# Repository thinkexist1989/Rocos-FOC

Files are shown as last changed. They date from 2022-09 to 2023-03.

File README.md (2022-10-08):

# ROCOS FOC *for Motor Control*

:warning:这是一个FOC驱动器项目，目前正在开发中~

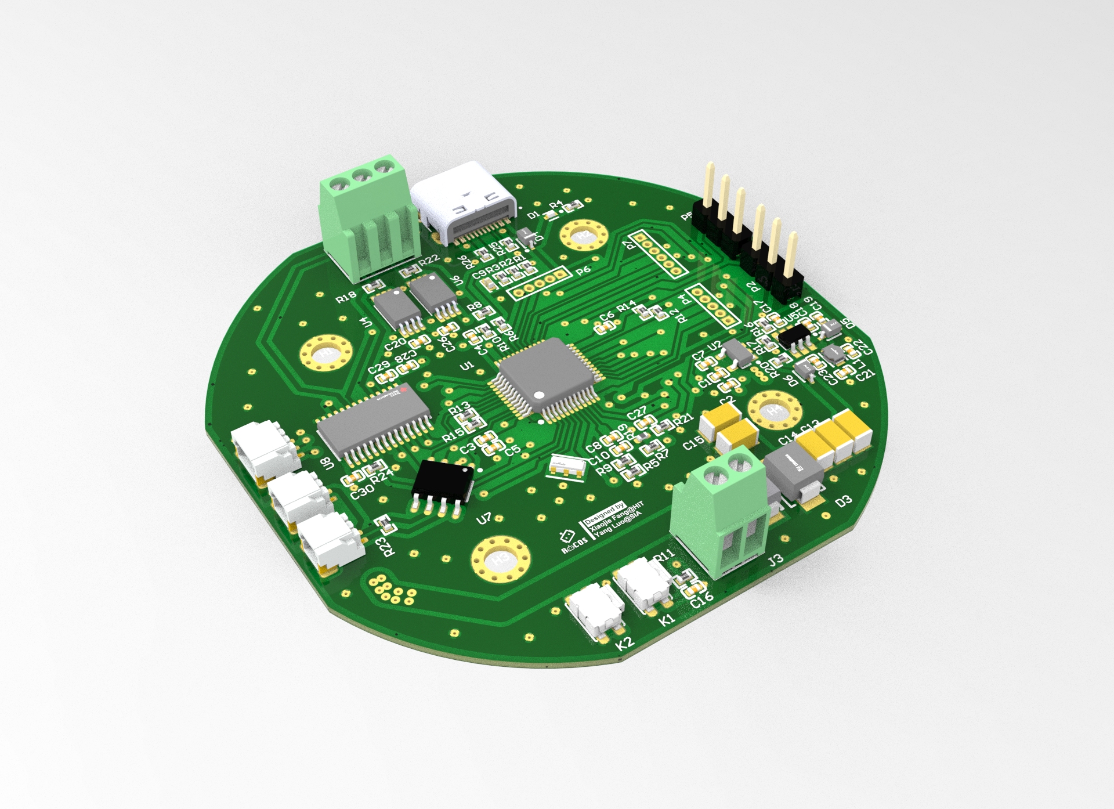
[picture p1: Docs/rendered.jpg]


驱动器采用的方案：

- **电机**：[GB6010云台电机](https://item.taobao.com/item.htm?spm=a1z0d.7625083.1998302264.6.5c5f4e6900plQJ&id=639378697535)，14对极，具体参数如下：
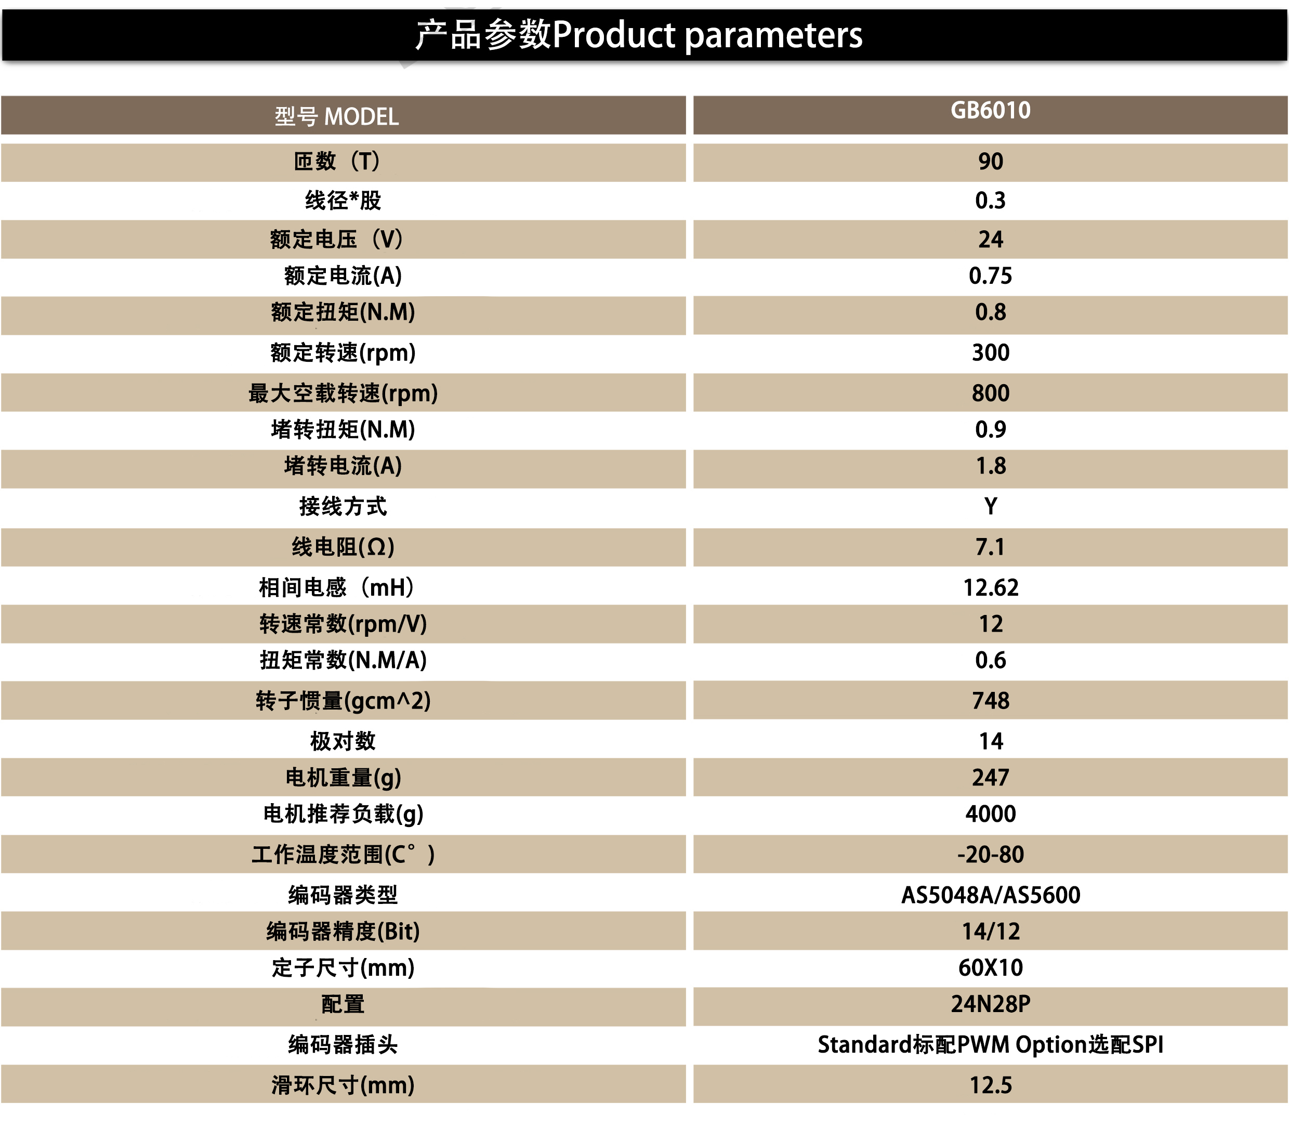
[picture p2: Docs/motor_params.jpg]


- **主控**：STM32F103CBT6
- **位置传感器**：AS5048A，SPI接口
- **驱动**：DRV8313
- **电流传感器**：INA240，线上检测（增益50V/V，采样电阻0.01R）

## 接口及尺寸定义

驱动器可以直接安装在电机尾部（电机尾部自带一块径向充磁的磁铁，AS5048A正对磁铁）

接口方面主要包括：

- USB-C接口（16pin）
- 电机三相接口，KF128-3p
- 电源接口， KF128-2p
- SW调试口， SH1.0-3p
- CAN总线接口，SH1.0-2p

其余引脚通过插针引出使用，具体见下图：

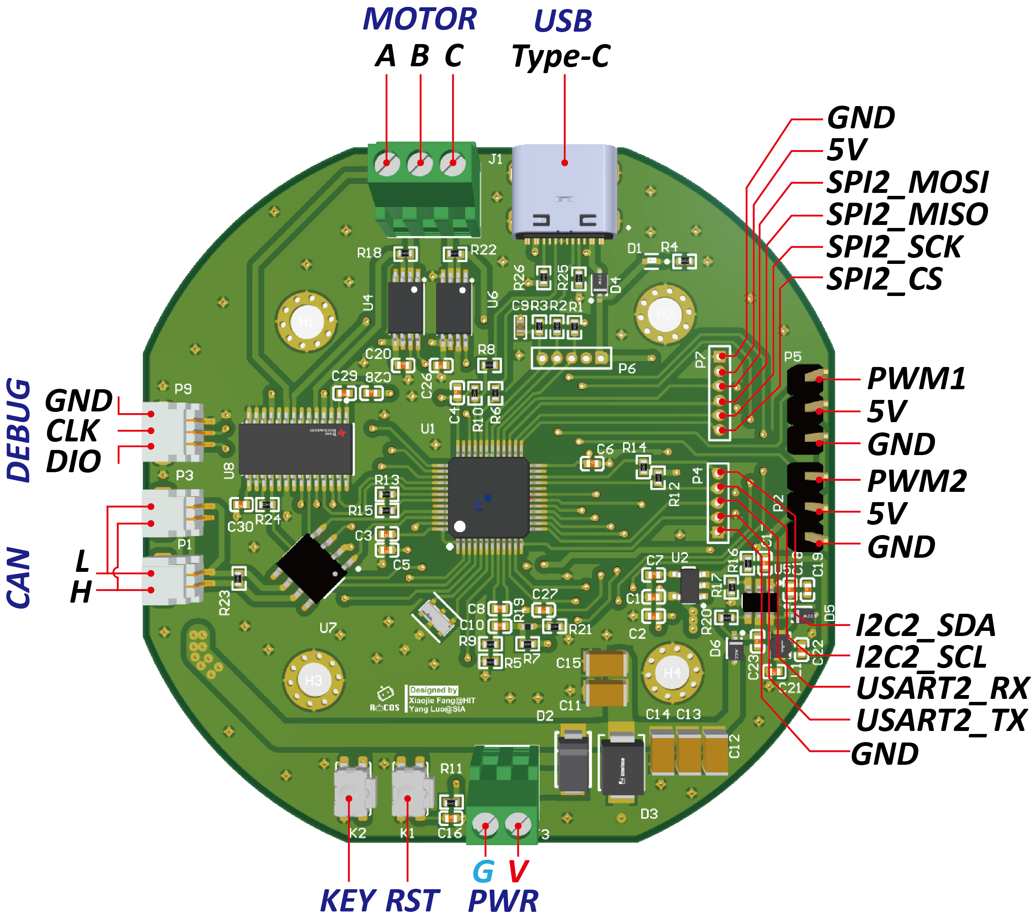
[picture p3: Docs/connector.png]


## 文件夹结构

```bash
Rocos-FOC
 ├── Firmware 驱动器固件代码
       ├── HAL_Version 基于STM32CubeMX和HAL库版本
       └── Platformio_Version 基于Platformio及Arduino版本
 ├── Hardware 硬件设计（原理图和PCB）
 ├── Model 驱动器三维模型Keyshots渲染文件
 ├── Docs  相关资料文档
 └── Utils 相关实用工具

```

## 参考

- [SimpleFOClibrary - Simple Field Oriented Control (FOC) library](https://github.com/simplefoc/Arduino-FOC)
- [Ctrl-FOC-Lite评估套件](https://github.com/peng-zhihui/Ctrl-FOC-Lite)
- [灯哥开源FOC双路无刷电机控制器](https://github.com/ToanTech/Deng-s-foc-controller)
- [dgm 电机驱动器简介](https://github.com/codenocold/dgm)
- [ODrive](https://github.com/odriverobotics/ODrive)

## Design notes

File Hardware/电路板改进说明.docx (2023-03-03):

# Rocos-foc电路改进说明

1. 增加了USB转串口模块，占用了原本留空的UART2接口：
2. 给CAN信号增加了终端电阻的开关，只需拨动开关即可实现工作模式的切换：
3. USB与CAN线增加了差分符号，可以使用altium designer提供的差分布线工具更快布线，并附带耦合检查功能
4. 调整了ABC三相导线的线序，方便布线，交换了原AC两项导线位置
5. 排针全部删去，换成了sh1.0接口
6. 固定孔网络改为NO NET，减少短路风险
7. 改变了按键朝向，方便按动
8. VCC走线大部分移到内电层，减少表层布线压力
9. 给晶振加了包地和铺铜挖空
10. 所有接口在正面标明了各引脚定义，方便查看

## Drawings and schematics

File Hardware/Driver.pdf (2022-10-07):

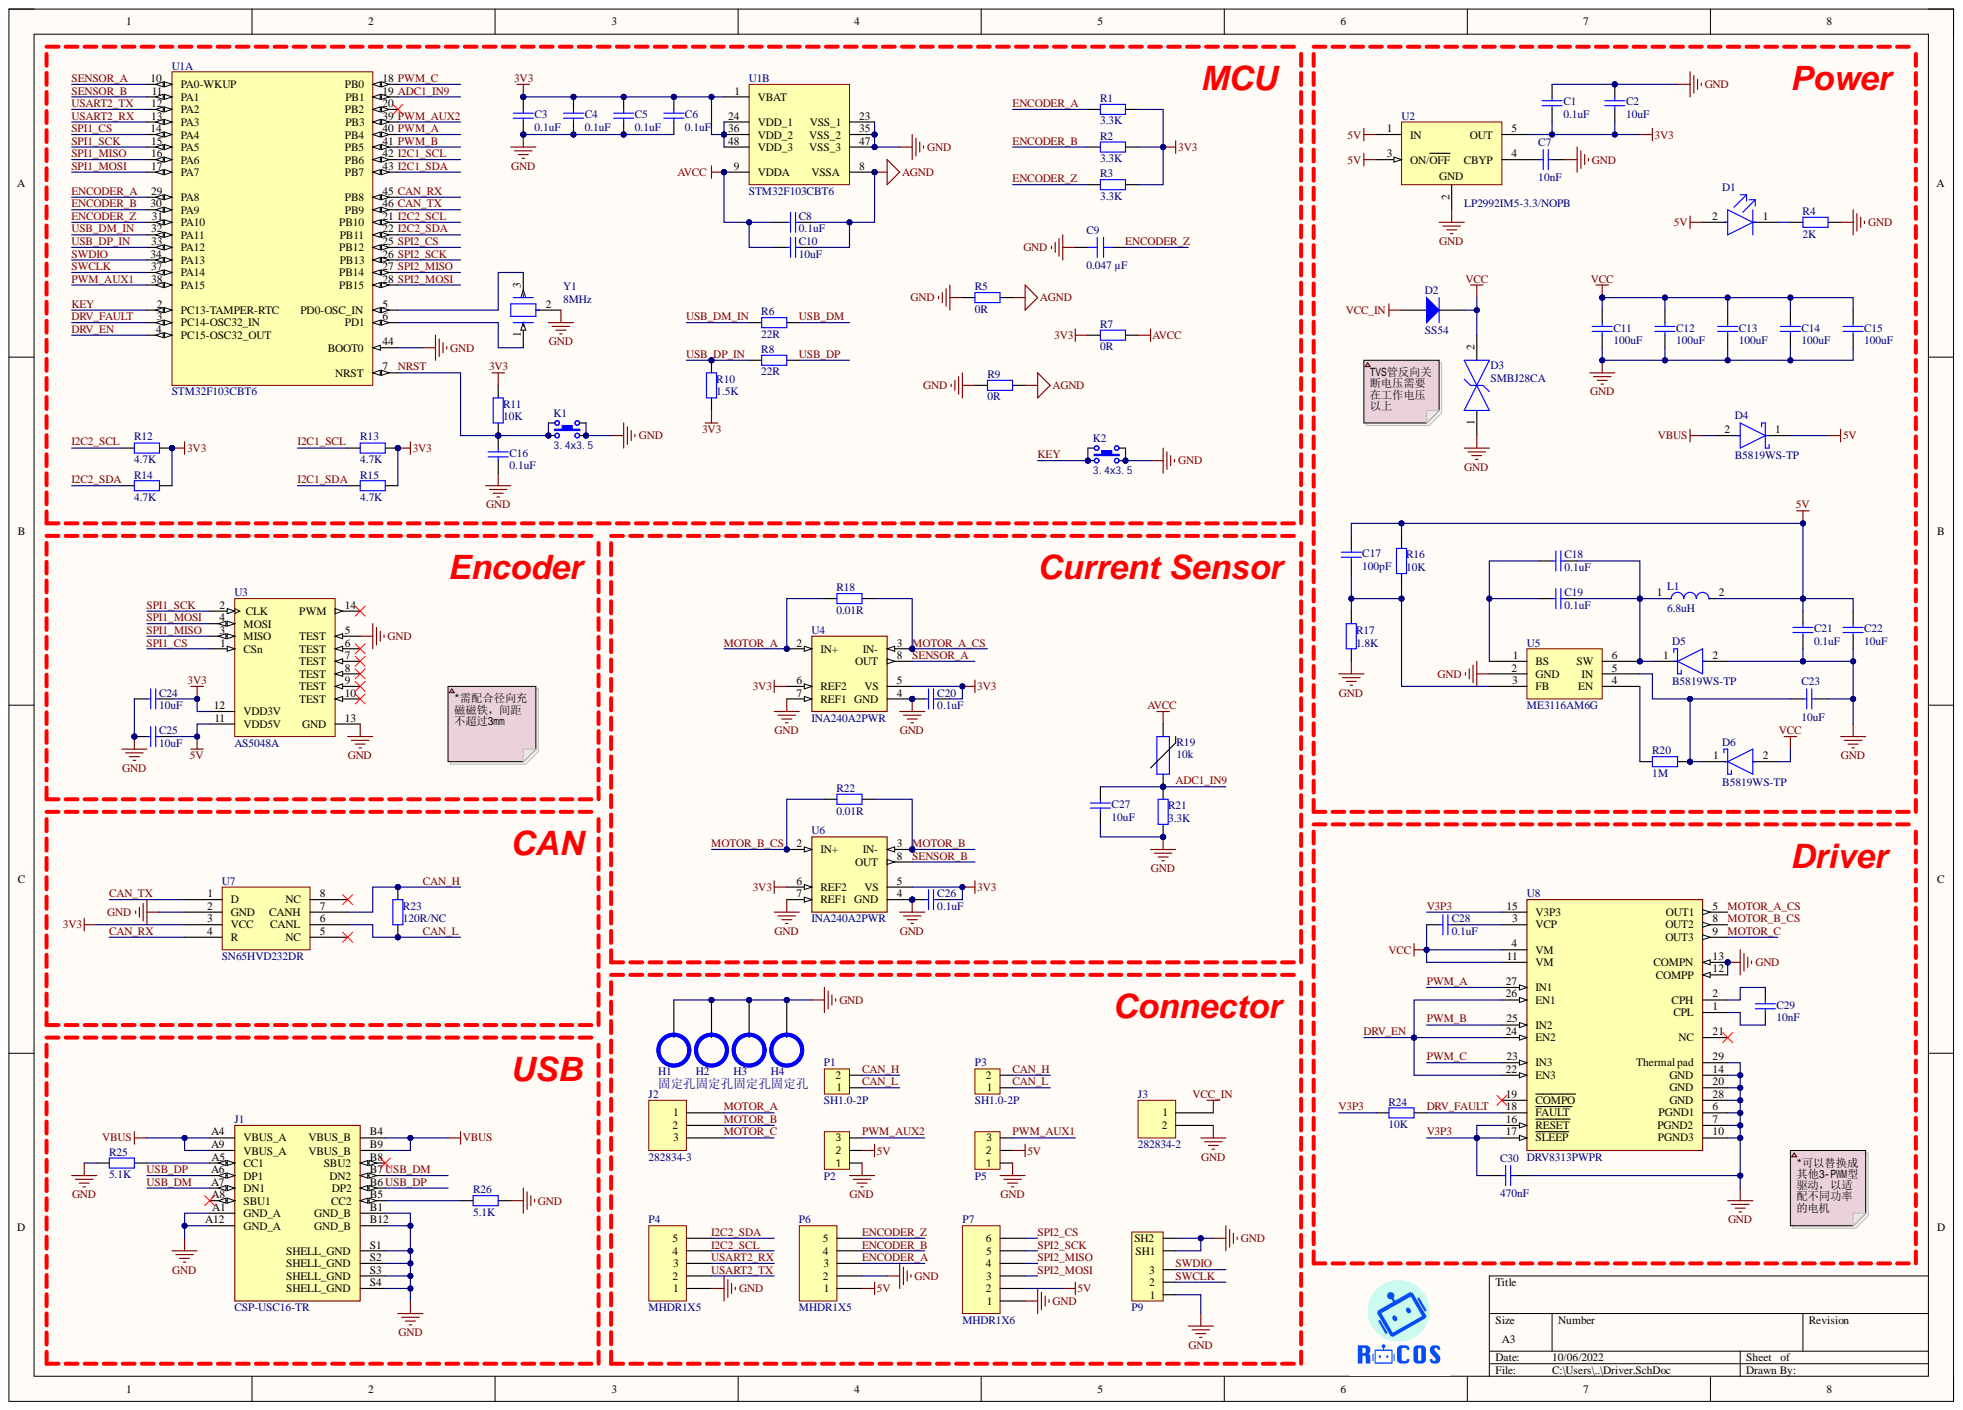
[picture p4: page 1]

TVS管反向关 断电压需要 在工作电压 以上

需配合径向充 磁磁铁，间距 不超过 mm

可以替换成 其他 PWM型 驱动，以适

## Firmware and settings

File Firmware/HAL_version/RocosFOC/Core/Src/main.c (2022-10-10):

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
/* Includes ------------------------------------------------------------------*/
#include "main.h"
#include "usb_device.h"

/* USER CODE BEGIN Includes */
#include "usbd_cdc_if.h"
/* USER CODE END Includes */

 ADC_HandleTypeDef hadc1;
DMA_HandleTypeDef hdma_adc1;

RTC_HandleTypeDef hrtc;

SPI_HandleTypeDef hspi1;

TIM_HandleTypeDef htim1;
TIM_HandleTypeDef htim2;
TIM_HandleTypeDef htim3;
TIM_HandleTypeDef htim4;

/* USER CODE BEGIN PV */

//!< for timestamp_us
unsigned long timer_counter = 0;

/* USER CODE END PV */

void SystemClock_Config(void);
static void MX_GPIO_Init(void);
static void MX_ADC1_Init(void);
static void MX_SPI1_Init(void);
static void MX_TIM1_Init(void);
static void MX_TIM3_Init(void);
static void MX_DMA_Init(void);
static void MX_TIM4_Init(void);
static void MX_RTC_Init(void);
static void MX_TIM2_Init(void);
/* USER CODE BEGIN PFP */
static void USB_Status_Init(void);
/* USER CODE END PFP */

/**
  * @brief  The application entry point.
  * @retval int
  */
int main(void)
{
  /* MCU Configuration--------------------------------------------------------*/

  /* Reset of all peripherals, Initializes the Flash interface and the Systick. */
  HAL_Init();

  /* Configure the system clock */
  SystemClock_Config();

  /* USER CODE BEGIN SysInit */
  USB_Status_Init();
  /* USER CODE END SysInit */

  /* Initialize all configured peripherals */
  MX_GPIO_Init();
  MX_ADC1_Init();
  MX_SPI1_Init();
  MX_TIM1_Init();
  MX_TIM3_Init();
  MX_USB_DEVICE_Init();
  MX_DMA_Init();
  MX_TIM4_Init();
  MX_RTC_Init();
  MX_TIM2_Init();
  /* USER CODE BEGIN 2 */
  //!< start pwm
  HAL_TIM_PWM_Start(&htim3, TIM_CHANNEL_1); // Motor A
  HAL_TIM_PWM_Start(&htim3, TIM_CHANNEL_2); // Motor B
  HAL_TIM_PWM_Start(&htim3, TIM_CHANNEL_3); // Motor C
  //!< for delay_us
  HAL_TIM_Base_Start(&htim2);
    HAL_TIM_Base_Start_IT(&htim4);
  TaskSetup();

  /* USER CODE END 2 */

  /* Infinite loop */
  /* USER CODE BEGIN WHILE */
  while (1)
  {
    /* USER CODE END WHILE */

    /* USER CODE BEGIN 3 */
    TaskDo();

  }
  /* USER CODE END 3 */
}

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
/* USER CODE BEGIN 4 */
static void USB_Status_Init(void) {
    GPIO_InitTypeDef GPIO_InitStruct = {0};

    /* GPIO Ports Clock Enable */
    __HAL_RCC_GPIOA_CLK_ENABLE();

    /*Configure GPIO pin Output Level */
    HAL_GPIO_WritePin(GPIOA, GPIO_PIN_11 | GPIO_PIN_12, GPIO_PIN_RESET);

    /*Configure GPIO pin : W25Q256_CS_Pin */
    GPIO_InitStruct.Pin = GPIO_PIN_11 | GPIO_PIN_12;
    GPIO_InitStruct.Mode = GPIO_MODE_OUTPUT_PP;
    GPIO_InitStruct.Pull = GPIO_PULLDOWN;
    GPIO_InitStruct.Speed = GPIO_SPEED_FREQ_LOW;
    HAL_GPIO_Init(GPIOA, &GPIO_InitStruct);

    HAL_Delay(20);
}

void HAL_TIM_PeriodElapsedCallback(TIM_HandleTypeDef *htim) {
//    usb_printf("timer_counter: %d", timer_counter);
    if(htim->Instance == htim4.Instance) {
        timer_counter ++;
    }
}

void _writeDutyCycle3PWM(float dc_a, float dc_b, float dc_c) {
    __HAL_TIM_SetCompare(&htim3, TIM_CHANNEL_1, dc_a*PWM_RANGE);
    __HAL_TIM_SetCompare(&htim3, TIM_CHANNEL_2, dc_b*PWM_RANGE);
    __HAL_TIM_SetCompare(&htim3, TIM_CHANNEL_3, dc_c*PWM_RANGE);
}

/* USER CODE END 4 */
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


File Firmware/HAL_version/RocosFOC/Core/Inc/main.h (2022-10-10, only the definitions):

#define KEY_Pin GPIO_PIN_13
#define KEY_GPIO_Port GPIOC
#define DRV_FAULT_Pin GPIO_PIN_14
#define DRV_FAULT_GPIO_Port GPIOC
#define DRV_EN_Pin GPIO_PIN_15
#define DRV_EN_GPIO_Port GPIOC
#define SENSOR_A_Pin GPIO_PIN_0
#define SENSOR_A_GPIO_Port GPIOA
#define SENSOR_B_Pin GPIO_PIN_1
#define SENSOR_B_GPIO_Port GPIOA
#define SPI1_CS_Pin GPIO_PIN_4
#define SPI1_CS_GPIO_Port GPIOA
#define PWM_C_Pin GPIO_PIN_0
#define PWM_C_GPIO_Port GPIOB
#define SPI2_CS_Pin GPIO_PIN_12
#define SPI2_CS_GPIO_Port GPIOB
#define ENCODER_A_Pin GPIO_PIN_8
#define ENCODER_A_GPIO_Port GPIOA
#define ENCODER_B_Pin GPIO_PIN_9
#define ENCODER_B_GPIO_Port GPIOA
#define ENCODER_Z_Pin GPIO_PIN_10
#define ENCODER_Z_GPIO_Port GPIOA
#define PWM_AUX1_Pin GPIO_PIN_15
#define PWM_AUX1_GPIO_Port GPIOA
#define PWM_AUX2_Pin GPIO_PIN_3
#define PWM_AUX2_GPIO_Port GPIOB
#define PWM_A_Pin GPIO_PIN_4
#define PWM_A_GPIO_Port GPIOB
#define PWM_B_Pin GPIO_PIN_5
#define PWM_B_GPIO_Port GPIOB
#define PWM_RANGE 1800 //!< pwm range 1800 by Yang Luo

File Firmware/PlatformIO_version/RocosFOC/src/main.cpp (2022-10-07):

#include "Arduino.h"
#include "SimpleFOC.h"
#include "USBSerial.h"
#include "SPI.h"
#include "SimpleFOCDrivers.h"
#include "encoders/as5048a/MagneticSensorAS5048A.h"

#define SPI_MISO   PA6
#define SPI_MOSI   PA7
#define SPI_SCLK   PA5
#define SPI_CS     PA4

#define PWM_A      PB4
#define PWM_B      PB5
#define PWM_C      PB0
#define DRV_EN     PC15

#define SENSOR_A   PA0
#define SENSOR_B   PA1

// MagneticSensorAS5048A sensor1(SPI_CS, false); // false - 是否开启快速读取模式
// MagneticSensorSPI sensor = MagneticSensorSPI(AS5048_SPI, SPI_CS);
// SPIClass spi_1(SPI_MOSI, SPI_MISO, SPI_SCLK);

//电机
BLDCMotor motor1 = BLDCMotor(14);
BLDCDriver3PWM driver1 = BLDCDriver3PWM(PB4, PB5, PB0, DRV_EN);

InlineCurrentSense current_sense1 = InlineCurrentSense(0.01, 50.0, SENSOR_A, SENSOR_B);

//目标变量
float target_velocity = 5;

Commander command = Commander(Serial);
void doTarget(char* cmd) { command.scalar(&target_velocity, cmd); }
void onMotor(char* cmd){ command.motor(&motor1,cmd); }      // 串口控制指令：电机


void setup() {
  //
  driver1.pwm_frequency = 10000; // 20kHz
  //
  driver1.voltage_power_supply = 12;
  driver1.voltage_limit = 12;

  driver1.init();

  driver1.enable();

  _delay(1000);



}

void loop() {
  // put your main code here, to run repeatedly:

  // iterative setting FOC phase voltage
  // motor1.loopFOC();

  // iterative function setting the outter loop target
  driver1.setPwm(5, 4, 3);

  // user communication
  // motor1.monitor();

  // command.run();
  _delay(1000);

}  

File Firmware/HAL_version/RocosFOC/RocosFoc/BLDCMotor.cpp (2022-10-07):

#include "BLDCMotor.h"
#include "./communication/SimpleFOCDebug.h"

#include <math.h>

// BLDCMotor( int pp , float R)
// - pp            - pole pair number
// - R             - motor phase resistance
// - KV            - motor kv rating (rmp/v)
BLDCMotor::BLDCMotor(int pp, float _R, float _KV)
: FOCMotor()
{
  // save pole pairs number
  pole_pairs = pp;
  // save phase resistance number
  phase_resistance = _R;
  // save back emf constant KV = 1/KV
  KV_rating = _KV;

  // torque control type is voltage by default
  torque_controller = TorqueControlType::voltage;
}


/**
	Link the driver which controls the motor
*/
void BLDCMotor::linkDriver(BLDCDriver* _driver) {
  driver = _driver;
}

// init hardware pins
void BLDCMotor::init() {
  if (!driver || !driver->initialized) {
    motor_status = FOCMotorStatus::motor_init_failed;
    SIMPLEFOC_DEBUG("MOT: Init not possible, driver not initialized");
    return;
  }
  motor_status = FOCMotorStatus::motor_initializing;
  SIMPLEFOC_DEBUG("MOT: Init");

  // sanity check for the voltage limit configuration
  if(voltage_limit > driver->voltage_limit) voltage_limit =  driver->voltage_limit;
  // constrain voltage for sensor alignment
  if(voltage_sensor_align > voltage_limit) voltage_sensor_align = voltage_limit;

  // update the controller limits
  if(current_sense){
    // current control loop controls voltage
    PID_current_q.limit = voltage_limit;
    PID_current_d.limit = voltage_limit;
  }
  if(_isset(phase_resistance) || torque_controller != TorqueControlType::voltage){
    // velocity control loop controls current
    PID_velocity.limit = current_limit;
  }else{
    // velocity control loop controls the voltage
    PID_velocity.limit = voltage_limit;
  }
  P_angle.limit = velocity_limit;

  _delay(500);
  // enable motor
  SIMPLEFOC_DEBUG("MOT: Enable driver.");
  enable();
  _delay(500);
  motor_status = FOCMotorStatus::motor_uncalibrated;
}


// disable motor driver
void BLDCMotor::disable()
{
  // set zero to PWM
  driver->setPwm(0, 0, 0);
  // disable the driver
  driver->disable();
  // motor status update
  enabled = 0;
}
// enable motor driver
void BLDCMotor::enable()
{
  // enable the driver
  driver->enable();
  // set zero to PWM
  driver->setPwm(0, 0, 0);
  // motor status update
  enabled = 1;
}

/**
  FOC functions
*/
// FOC initialization function
int  BLDCMotor::initFOC( float zero_electric_offset, Direction _sensor_direction) {
  int exit_flag = 1;

  motor_status = FOCMotorStatus::motor_calibrating;

  // align motor if necessary
  // alignment necessary for encoders!
  if(_isset(zero_electric_offset)){
    // abosolute zero offset provided - no need to align
    zero_electric_angle = zero_electric_offset;
    // set the sensor direction - default CW
    sensor_direction = _sensor_direction;
  }

  // sensor and motor alignment - can be skipped
  // by setting motor.sensor_direction and motor.zero_electric_angle
  _delay(500);
  if(sensor){
    exit_flag *= alignSensor();
    // added the shaft_angle update
    sensor->update();
    shaft_angle = shaftAngle();
  }else 
    SIMPLEFOC_DEBUG("MOT: No sensor.");

  // aligning the current sensor - can be skipped
  // checks if driver phases are the same as current sense phases
  // and checks the direction of measuremnt.
  _delay(500);
  if(exit_flag){
    if(current_sense) exit_flag *= alignCurrentSense();
    else SIMPLEFOC_DEBUG("MOT: No current sense.");
  }

  if(exit_flag){
    SIMPLEFOC_DEBUG("MOT: Ready.");
    motor_status = FOCMotorStatus::motor_ready;
  }else{
    SIMPLEFOC_DEBUG("MOT: Init FOC failed.");
    motor_status = FOCMotorStatus::motor_calib_failed;
    disable();
  }

  return exit_flag;
}

// Calibarthe the motor and current sense phases
int BLDCMotor::alignCurrentSense() {
  int exit_flag = 1; // success

  SIMPLEFOC_DEBUG("MOT: Align current sense.");

  // align current sense and the driver
  exit_flag = current_sense->driverAlign(voltage_sensor_align);
  if(!exit_flag){
    // error in current sense - phase either not measured or bad connection
    SIMPLEFOC_DEBUG("MOT: Align error!");
    exit_flag = 0;
  }else{
    // output the alignment status flag
    SIMPLEFOC_DEBUG("MOT: Success: ", exit_flag);
  }

  return exit_flag > 0;
}

// Encoder alignment to electrical 0 angle
int BLDCMotor::alignSensor() {
  int exit_flag = 1; //success
  SIMPLEFOC_DEBUG("MOT: Align sensor.");

  // check if sensor needs zero search
  if(sensor->needsSearch()) exit_flag = absoluteZeroSearch();
  // stop init if not found index
  if(!exit_flag) return exit_flag;

  // if unknown natural direction
  if(!_isset(sensor_direction)){

    // find natural direction
    // move one electrical revolution forward
    for (int i = 0; i <=500; i++ ) {
      float angle = _3PI_2 + _2PI * i / 500.0f;
      setPhaseVoltage(voltage_sensor_align, 0,  angle);
	  sensor->update();
      _delay(2);
    }
    // take and angle in the middle
    sensor->update();
    float mid_angle = sensor->getAngle();
    // move one electrical revolution backwards
    for (int i = 500; i >=0; i-- ) {
      float angle = _3PI_2 + _2PI * i / 500.0f ;
      setPhaseVoltage(voltage_sensor_align, 0,  angle);
	  sensor->update();
      _delay(2);
    }
    sensor->update();
    float end_angle = sensor->getAngle();
    setPhaseVoltage(0, 0, 0);
    _delay(200);
    // determine the direction the sensor moved
    if (mid_angle == end_angle) {
      SIMPLEFOC_DEBUG("MOT: Failed to notice movement");
      return 0; // failed calibration
    } else if (mid_angle < end_angle) {
      SIMPLEFOC_DEBUG("MOT: sensor_direction==CCW");
      sensor_direction = Direction::CCW;
    } else{
      SIMPLEFOC_DEBUG("MOT: sensor_direction==CW");
      sensor_direction = Direction::CW;
    }
    // check pole pair number
    float moved =  fabs(mid_angle - end_angle);
    if( fabs(moved*pole_pairs - _2PI) > 0.5f ) { // 0.5f is arbitrary number it can be lower or higher!
      SIMPLEFOC_DEBUG("MOT: PP check: fail - estimated pp: ", _2PI/moved);
    } else 
      SIMPLEFOC_DEBUG("MOT: PP check: OK!");

  } else SIMPLEFOC_DEBUG("MOT: Skip dir calib.");

  // zero electric angle not known
  if(!_isset(zero_electric_angle)){
    // align the electrical phases of the motor and sensor
    // set angle -90(270 = 3PI/2) degrees
    setPhaseVoltage(voltage_sensor_align, 0,  _3PI_2);
    _delay(700);
    // read the sensor
    sensor->update();
    // get the current zero electric angle
    zero_electric_angle = 0;
    zero_electric_angle = electricalAngle();
    //zero_electric_angle =  _normalizeAngle(_electricalAngle(sensor_direction*sensor->getAngle(), pole_pairs));
    _delay(20);
    if(monitor_port){
      SIMPLEFOC_DEBUG("MOT: Zero elec. angle: ", zero_electric_angle);
    }
    // stop everything
    setPhaseVoltage(0, 0, 0);
    _delay(200);
  }else SIMPLEFOC_DEBUG("MOT: Skip offset calib.");
  return exit_flag;
}
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

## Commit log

2022-09-09 房教授板子+丝印层小改动
    [Driver.PcbLib, Driver.SchDoc, Rocos-FOC.PrjPcb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]
2022-09-15 整理了一下仓库文件结构
    [Driver.PcbLib, Driver.SchDoc, Rocos-FOC.PrjPcb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]
2022-09-15 新增丝印层标记
2022-09-17 Add CLion-STM32 Project
2022-09-23 USB test passed!
    注意USB和CAN不能同时初始化，如果也开启了CAN，则需要HAL_CAN_DeInit()来禁用CAN，否则USB会显示无法识别设备
    [daplink.cfg, stlink.cfg]
2022-09-24 AS5048A SPI test pass :ok: !
    磁编码芯片测试通过
2022-10-01 Center align PWM test pass! :ok:
    利用TIM2 CH1测试20kHz中心对齐PWM通过
2022-10-05 delete SimpleFOC Library
    可以在platformio.ini中配置lib_deps来引入SimpleFOC
2022-10-07 Fix bugs
    发现stm32f103的外设不能全部初始化，会导致PWM输出异常
2022-10-09 Update
    在driver的init中配置initialized为true
2022-10-09 Fix Bugs
    协议解析有点问题
2022-10-10 Update
    1. 在.ioc中关闭了一些没用到的外设，包括CAN(因为和USB有冲突)
    2. 修改usbd_cdc.c中的USBD_CDC_DataIn()函数
    3. 测试过已经可以连续发送，但command中反馈的还是有问题，协议可能需要手动修改一下
    [RocosFOC.ioc, main.c, main.h]
2022-10-10 :warning: modified commander
    修改了Commander命令发送，尚未全部完成
2022-10-11 Modified print function call
    [stlink.cfg]
2023-03-03 改进电路板，详见电路板改进说明
    [Driver.SchDoc, ROCOS-FOC_V2.0.PcbLib, Rocos-FOC.PrjPcb]

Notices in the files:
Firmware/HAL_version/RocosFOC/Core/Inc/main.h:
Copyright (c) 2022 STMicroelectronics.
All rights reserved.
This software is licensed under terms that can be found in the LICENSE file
